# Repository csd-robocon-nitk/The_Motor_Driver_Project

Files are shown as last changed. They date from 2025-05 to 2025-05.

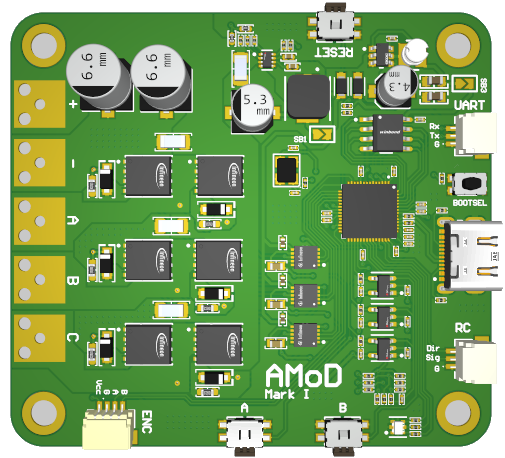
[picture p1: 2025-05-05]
Design/model.png

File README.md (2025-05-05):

# The Motor Driver Project

This project involves creating a smart electronic speed controller (ESC) for both brushed and brushless DC motors.

## Technologies Used

Tech Used

## Team Members

1. [Joel Jojo Painuthara](https://github.com/JoelJojoP)
2. [Sai Aswin Madhavan](https://github.com/MSaiAswin)
3. [Suhas R P](https://github.com/Suhas19822)

## License

This repository is licensed under the [BSD 3-Clause License](/LICENSE)

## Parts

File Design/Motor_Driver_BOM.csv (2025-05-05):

Line # | Quantity | Designator | Name | Footprint | Manufacturer Part Number 1 | Manufacturer 1 | Description
 | 10 | C1, C3, C4, C5, C6, C7, C8, C9, C11, C12 | 0.1 µF | CAP 0201_0603 | 885012104003 | Wurth Electronics | CAP CER 0.1UF 6.3V X5R 0201
 | 2 | C2, C10 | 1 µF | CAP 0201_0603 | 885012104011 | Wurth Electronics | CAP CER 1UF 6.3V X5R 0201
 | 2 | C13, C14 | 15 pF | CAP 0201_0603 | 885012004006 | Wurth Electronics | CAP CER 15PF 25V C0G/NP0 0201
 | 1 | C15 | 0.1 µF | CAP 0402_1005 | 885012205085 | Wurth Electronics | CAP CER 0.1UF 25V X7R 0402
 | 4 | C16, C38, C39, C40 | 10 µF | CAP 1206_3216 - 0.8MM | 885012108022 | Wurth Electronics | CAP CER 10UF 50V X5R 1206
 | 1 | C17 | 33 µF | CAP ALSMD 5.3MM H5.4MM | EEE-1CA330WAR | Panasonic | CAP ALUM 33UF 20% 16V SMD
 | 1 | C18 | 0.033 µF | CAP 0402_1005 | 885012205015 | Wurth Electronics | CAP CER 0.033UF 10V X7R 0402
 | 1 | C19 | 0.1 µF | CAP 0201_0603 | 885012104001 | Wurth Electronics | CAP CER 0.1UF 16V X5R 0201
 | 2 | C20, C21 | 100 µF | CAP ALSMD 6.6MM H8.0MM | EEEFK1V101XP | Panasonic | CAP ALUM 100UF 20% 35V SMD
 | 1 | C22 | 10 µF | CAP ALSMD 4.3MM H5.4MM | 865060340001 | Wurth Electronics | CAP ALUM 10UF 20% 16V SMD
 | 2 | C23, C24 | 22 µF | MURATA GRM188 0603_1608 | GRM188R60J226MEA0D | Murata | CAP CER 22UF 6.3V X5R 0603
 | 3 | C25, C26, C29 | 0.22 µF | CAP 0603_1608 | 885012206073 | Wurth Electronics | CAP CER 0.22UF 25V X7R 0603
 | 3 | C27, C28, C30 | 1 µF | MURATA GRM155 0402_1005 | GRM155R61E105KA12D | Murata | CAP CER 1UF 25V X5R 0402
 | 7 | C31, C32, C33, C34, C35, C36, C37 | 1000 pF | CAP 0201_0603 | 885012204006 | Wurth Electronics | CAP CER 1000PF 25V X7R 0201
 | 1 | D1 | 19-337C/RSBHGHC-A88/4T | FP-19-337C-RSBHGHC-A88-4T-MFG | 19-337C/RSBHGHC-A88/4T | Everlight | LED Tri-Color 468nm/518nm/632nm 6-Pin SMD-B T/R
 | 2 | D2, D3 | RB160VAM-60TR | RB160VAM-60TR-Footprint-1 | RB160VAM-60TR | Rohm | DIODE SCHOTTKY 60V 1A TUMD2M
 | 6 | D4, D5, D6, D7, D8, D9 | 1N5819HW1-7-F | SOD123F | 1N5819HW1-7-F | Diodes | DIODE SBR 40V 1A SOD123F
 | 1 | J2 | DX07S016JA1R1500 | FP-DX07S016JA1R1500-MFG | DX07S016JA1R1500 | JAE Electronics | USB Connector, 16 Contact(s), Female, Right Angle, Surface Mount Terminal, Locking, Receptacle
 | 1 | L1 | SRP5020TA-8R2M | SRP5020TA-8R2M-Footprint-1 | SRP5020TA-8R2M | Bourns | Ind Chip Power Shielded Wirewound 8.2uH 20% 100KHz 21Q-Factor Metal 2.3A T/R
 | 1 | L2 | SDR0302-3R9ML | SDR0302-3R9ML-Footprint-1 | SDR0302-3R9ML | Bourns | Inductor Power Wirewound 3.9uH 20% 1KHz 24Q-Factor Ferrite 1.3A 120mOhm DCR T/R
 | 1 | P1 | SM04B-SRSS-TB(LF)(SN) | SM04B-SRSS-TB(LF)(SN)-Footprint-1 | SM04B-SRSS-TB | JST | Connector Header, Side Entry, SR Series, 4 Position, 1.00mm, 50V, Surface Mount, Tin, Natural
 | 2 | P2, P3 | SM03B-SRSS-TB(LF)(SN) | JST-SM03B-SRSS-TB_V | SM03B-SRSS-TB | JST | Connector Header, Side Entry, SR Series, 3 Position, 1.00mm, 50V, Surface Mount, Tin, Natural
 | 6 | Q1, Q2, Q3, Q4, Q5, Q6 | BSC027N06LS5ATMA1 | FP-PG-TDSON-8-MFG | BSC027N06LS5ATMA1 | Infineon | Transistor Mosfet N-ch 60V 100A 8-PIN Tdson T/r
 | 3 | R1, R2, R5 | 27 Ohms | YAGEO RES 0201_0603 | RC0201FR-0727RL | Yageo | RES 27 OHM 1% 1/20W 0201
 | 1 | R3 | 1 kOhms | YAGEO RES 0201_0603 | RC0201FR-131KL | Yageo | RES 1K OHM 1% 1/20W 0201
 | 1 | R4 | 75 Ohms | YAGEO RES 0201_0603 | RC0201FR0775RL | Yageo | RES 75 OHM 1% 1/20W 0201
 | 1 | R6 | 5.6 kOhms | YAGEO RES 0201_0603 | RC0201FR-135K6L | Yageo | RES 5.6K OHM 1% 1/20W 0201
 | 1 | R7 | 5.6 Ohms | YAGEO RES 0201_0603 | RC0201FR-075R6L | Yageo | RES 5.6 OHM 1% 1/20W 0201
 | 8 | R8, R17, R28, R31, R32, R33, R34, R35 | 10 kOhms | YAGEO RES 0201_0603 | RC0201FR-0710KL | Yageo | RES 10K OHM 1% 1/20W 0201
 | 2 | R9, R10 | 5.1 kOhms | YAGEO RES 0201_0603 | RC0201FR075K1L | Yageo | RES 5.1K OHM 1% 1/20W 0201
 | 1 | R11 | 68 kOhms | YAGEO RES 0402_1005 | RC0402FR-0768KL | Yageo | RES 68K OHM 1% 1/16W 0402
 | 1 | R12 | 10 kOhms | YAGEO RES 0402_1005 | RC0402FR-0710KL | Yageo | RES 10K OHM 1% 1/16W 0402
 | 1 | R13 | 309 kOhms | YAGEO RES 0201_0603 | RC0201FR-07309KL | Yageo | RES 309K OHM 1% 1/20W 0201
 | 1 | R14 | 130 kOhms | YAGEO RES 0201_0603 | RC0201JR-07130KL | Yageo | RES 130K OHM 5% 1/20W 0201
 | 1 | R15 | 38.3 kOhms | YAGEO RES 0201_0603 | RC0201FR-0738K3L | Yageo | RES 38.3K OHM 1% 1/20W 0201
 | 1 | R16 | 9.09 kOhms | YAGEO RES 0201_0603 | RC0201FR-079K09L | Yageo | RES 9.09K OHM 1% 1/20W 0201
 | 6 | R18, R19, R20, R21, R22, R23 | 10 Ohms | YAGEO RES 0603_1608 | RC0603JR-0710RL | Yageo | RES 10 OHM 5% 1/10W 0603
 | 6 | R24, R25, R26, R27, R29, R30 | 47 kOhms | YAGEO RES 0201_0603 | RC0201FR-0747KL | Yageo | RES 47K OHM 1% 1/20W 0201
 | 1 | R36 | 1 kOhms | YAGEO RES 0201_0603 | RC0201JR-071KP | Yageo | RES 1K OHM 5% 1/20W 0201
 | 3 | S1, S2, S3 | EVQ-PUC02K | PANASONIC EVQPUC | EVQ-PUC02K | Panasonic | SWITCH TACTILE SPST-NO 0.05A 12V
 | 1 | S4 | KMR741NG ULC LFS | C&K KMR7 | KMR741NGULCLFS | ITT C&K | SWITCH TACTILE SPST-NO 50MA 32V
 | 1 | U1 | RP2040 | QFN40P700X700X90-57N | SC0914(7) | Raspberry Pi | ARM Microcontrollers - MCU IC RP2040 (RP2B2) T&R, 500 (7" reel)
 | 1 | U2 | TPS62932DRLR | FP-DRL0008A-MFG | TPS62932DRLR | Texas Instruments | 3.8-V to 30-V input, 2-A, 200-kHz to 2.2-MHz, low-IQ synchronous buck converter in SOT-583 package 8-SOT-5X3 -40 to 150
 | 1 | U3 | AP63203WU-7 | FP-TSOT26-MFG | AP63203WU-7 | Diodes | AP63203 Series 3.3 V 2 A SMT Fixed Low IQ Synchronous Buck - TSOT-26
 | 3 | U4, U5, U6 | 2ED2732S01G | SON50P300X300X90-11N-1 | 2ED2732S01GXTMA1 | Infineon | Half Bridge SOI Gate Driver with Integrated Bootstrap Diode
 | 3 | U7, U8, U9 | LMV321IDBVR | FP-DBV0005A-IPC_B | LMV321IDBVR | Texas Instruments | Single, 5.5-V, 1-MHz, RRO operational amplifier 5-SOT-23 -40 to 125
 | 1 | U10 | W25Q16JVSNIQ | FP-W25Q16JVSNIQ_TR-IPC_B | W25Q16JVSNIQ TR | Winbond | NOR Flash Serial (SPI, Dual SPI, Quad SPI) 3V/3.3V 16M-bit 2M x 8 6ns Automotive 8-Pin SOIC N T/R
 | 1 | Y1 | 12MHz | ABRACON ABM8G | ABM8G-12.000MHZ-B4Y-T | Abracon | CRYSTAL 12.0000MHZ 10PF SMD

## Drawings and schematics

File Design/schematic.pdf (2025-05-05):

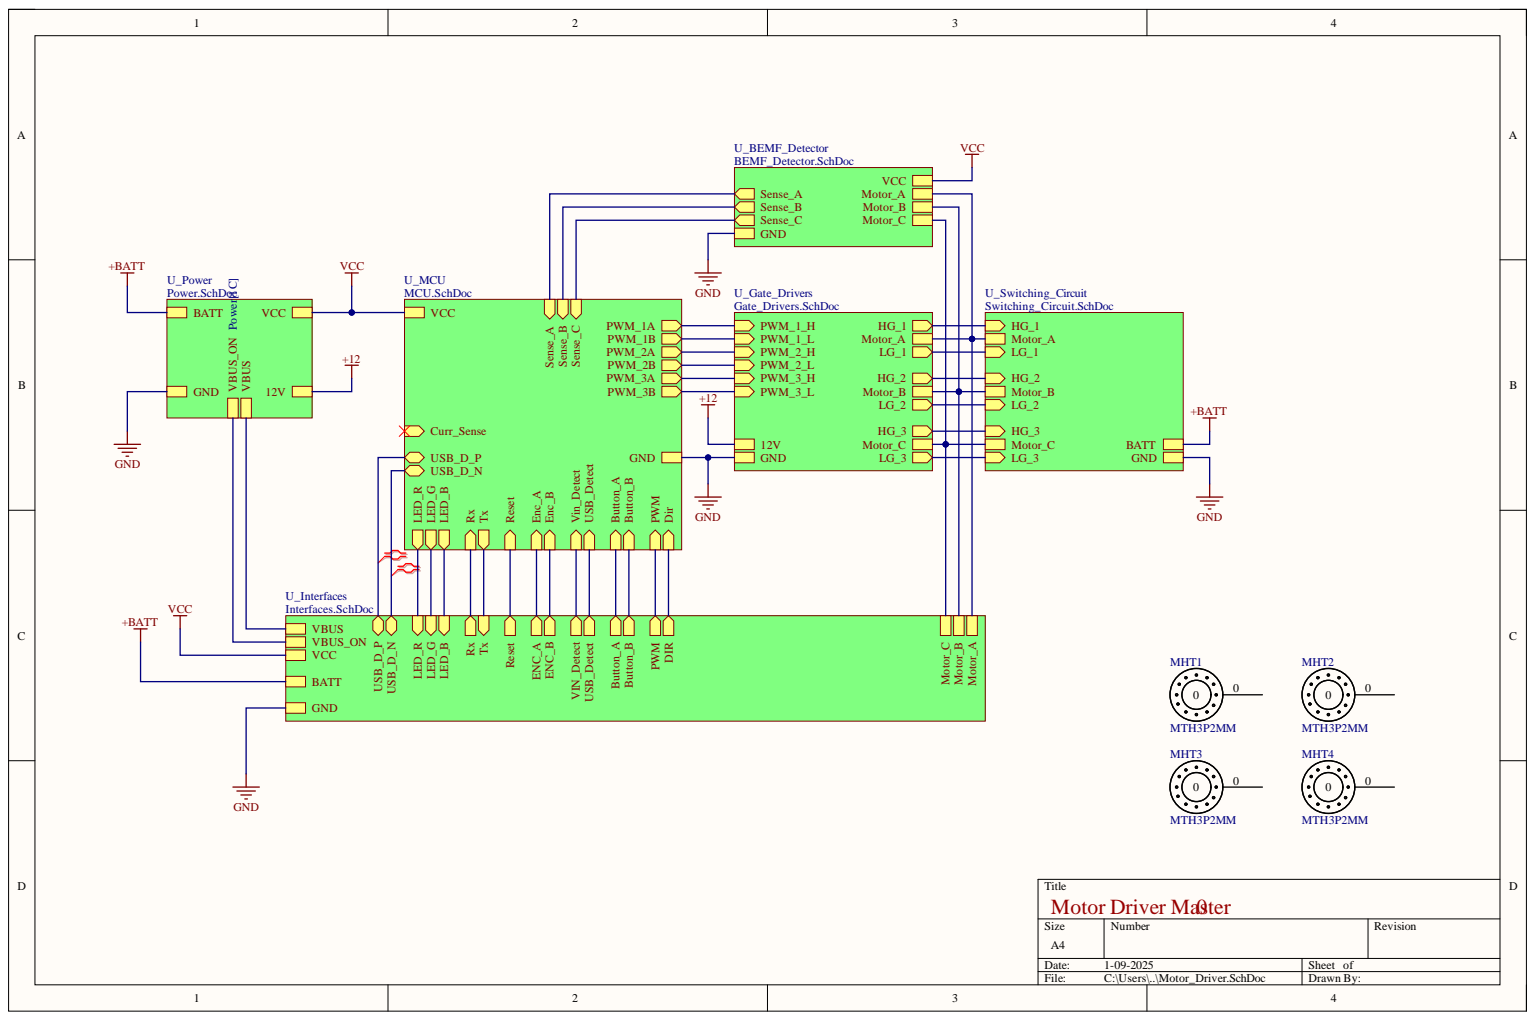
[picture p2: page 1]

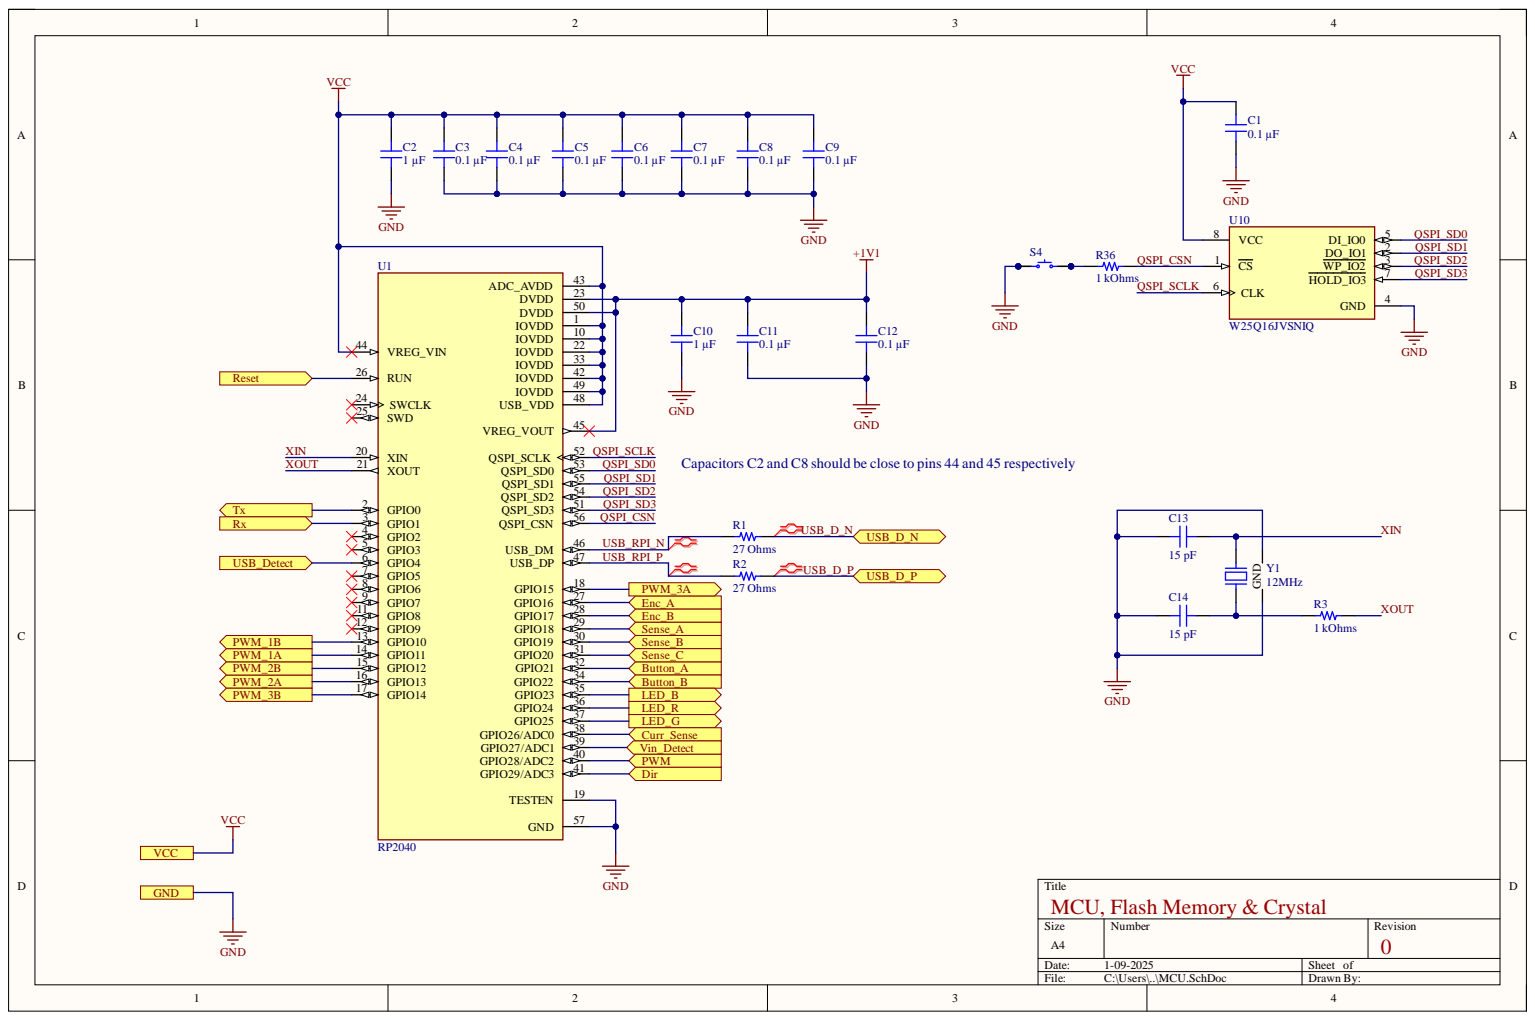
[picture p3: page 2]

Capacitors C2 and C8 should be close to pins 44 and 45 respectively

Title
MCU, Flash Memory & Crystal

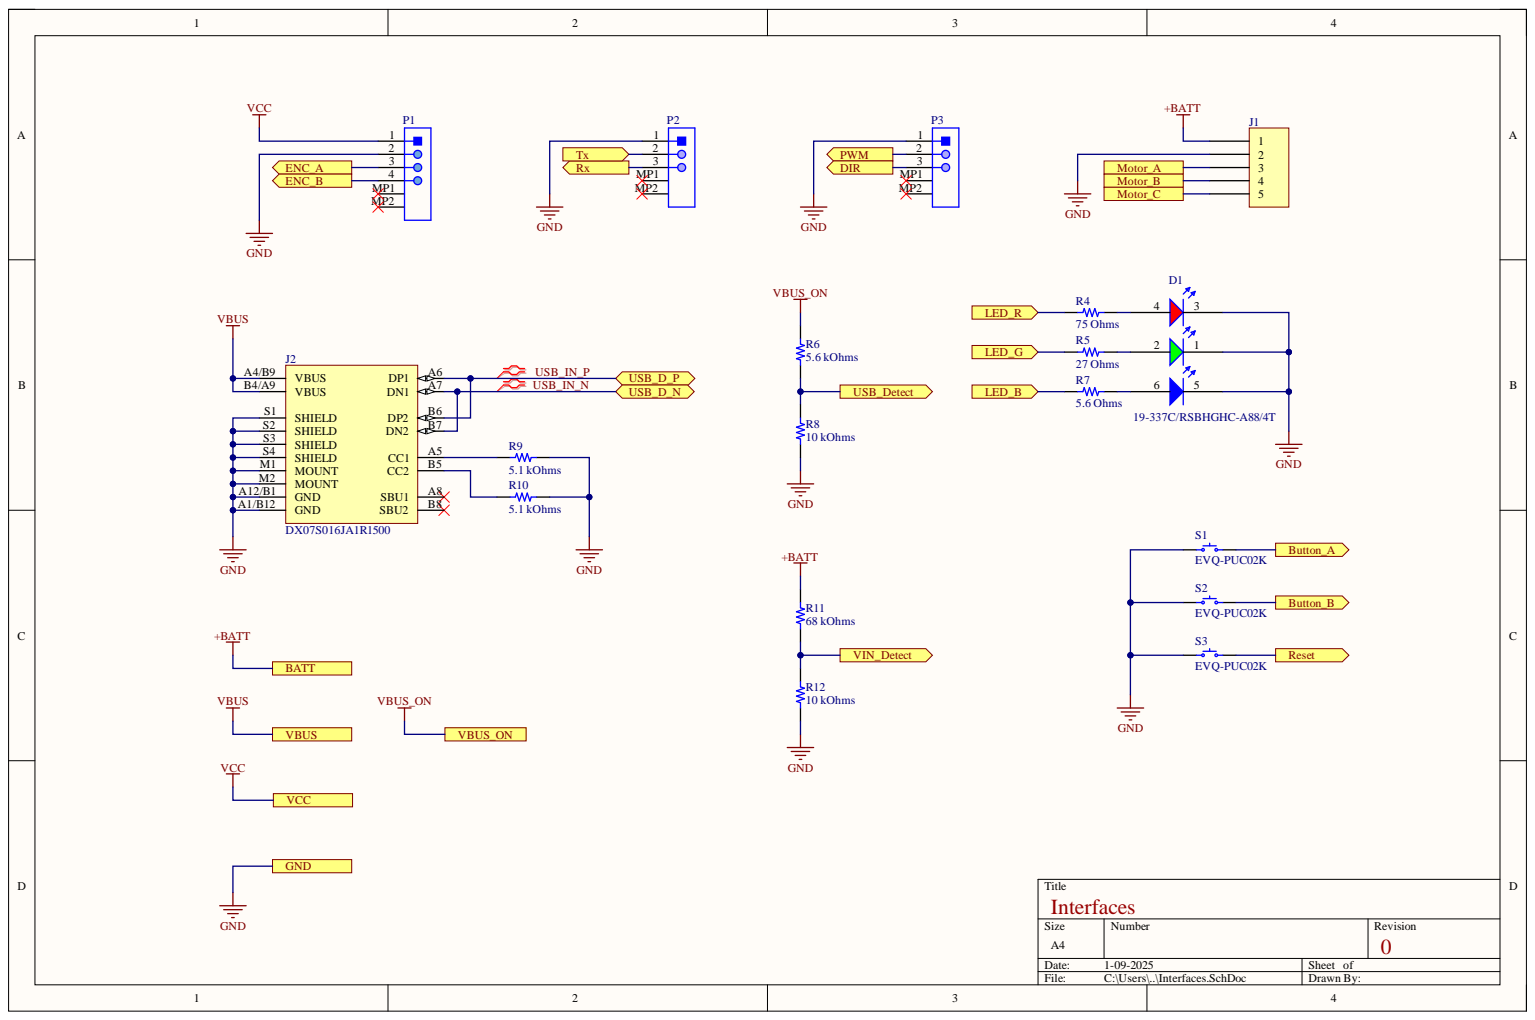
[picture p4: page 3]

SHIELD S2

SHIELD S4

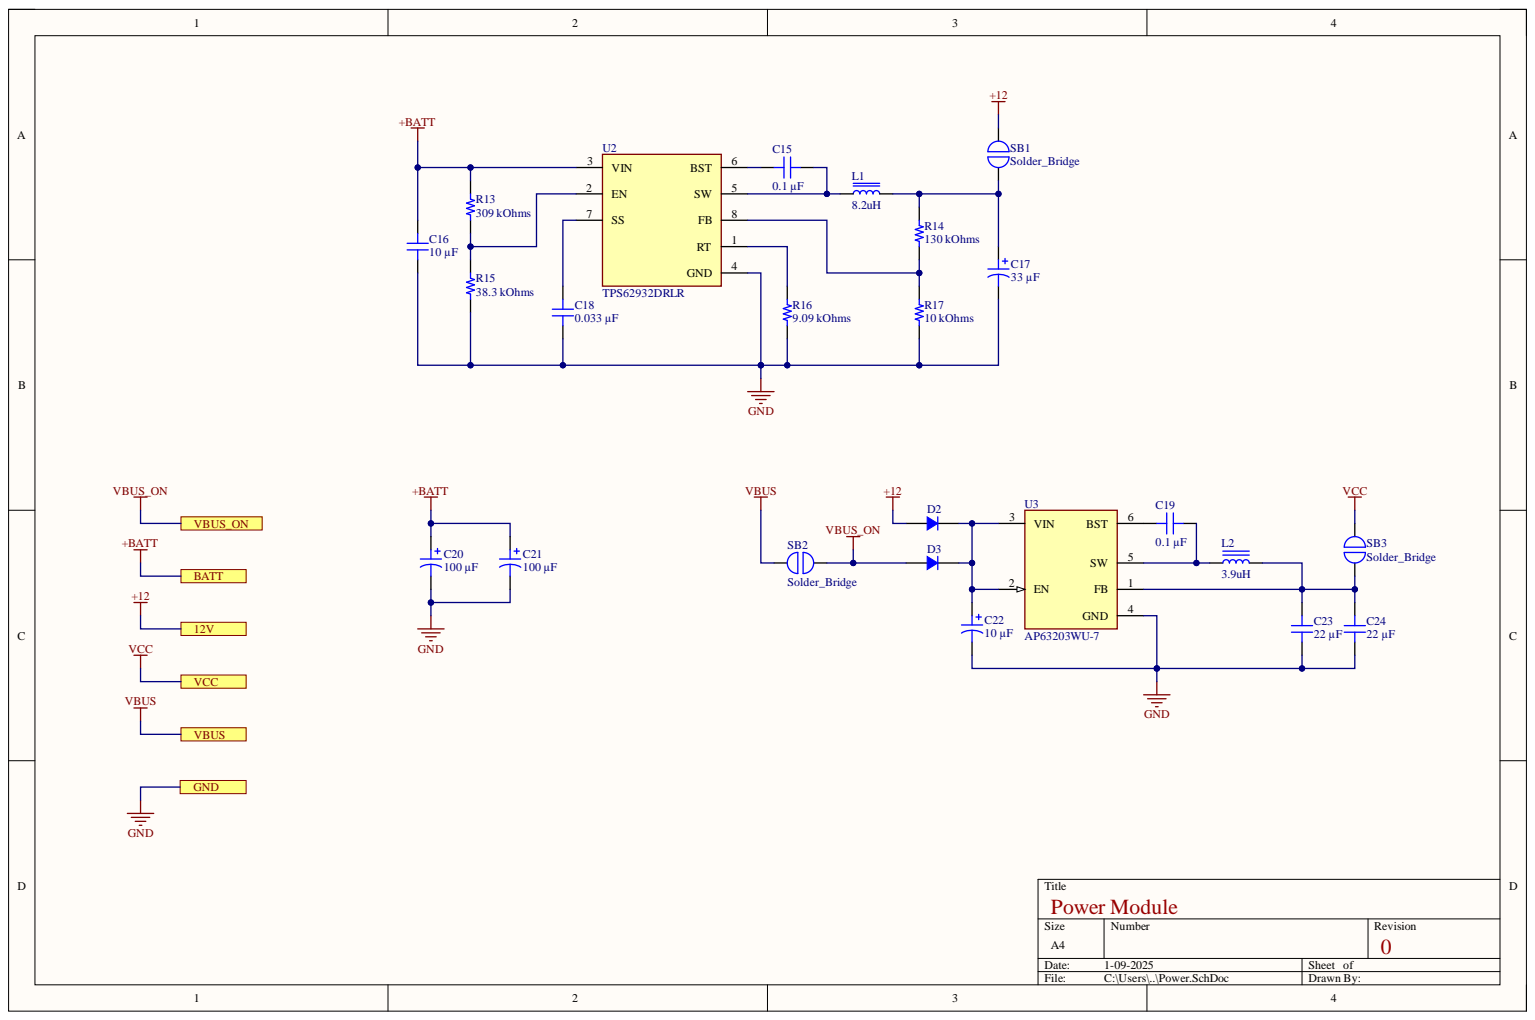
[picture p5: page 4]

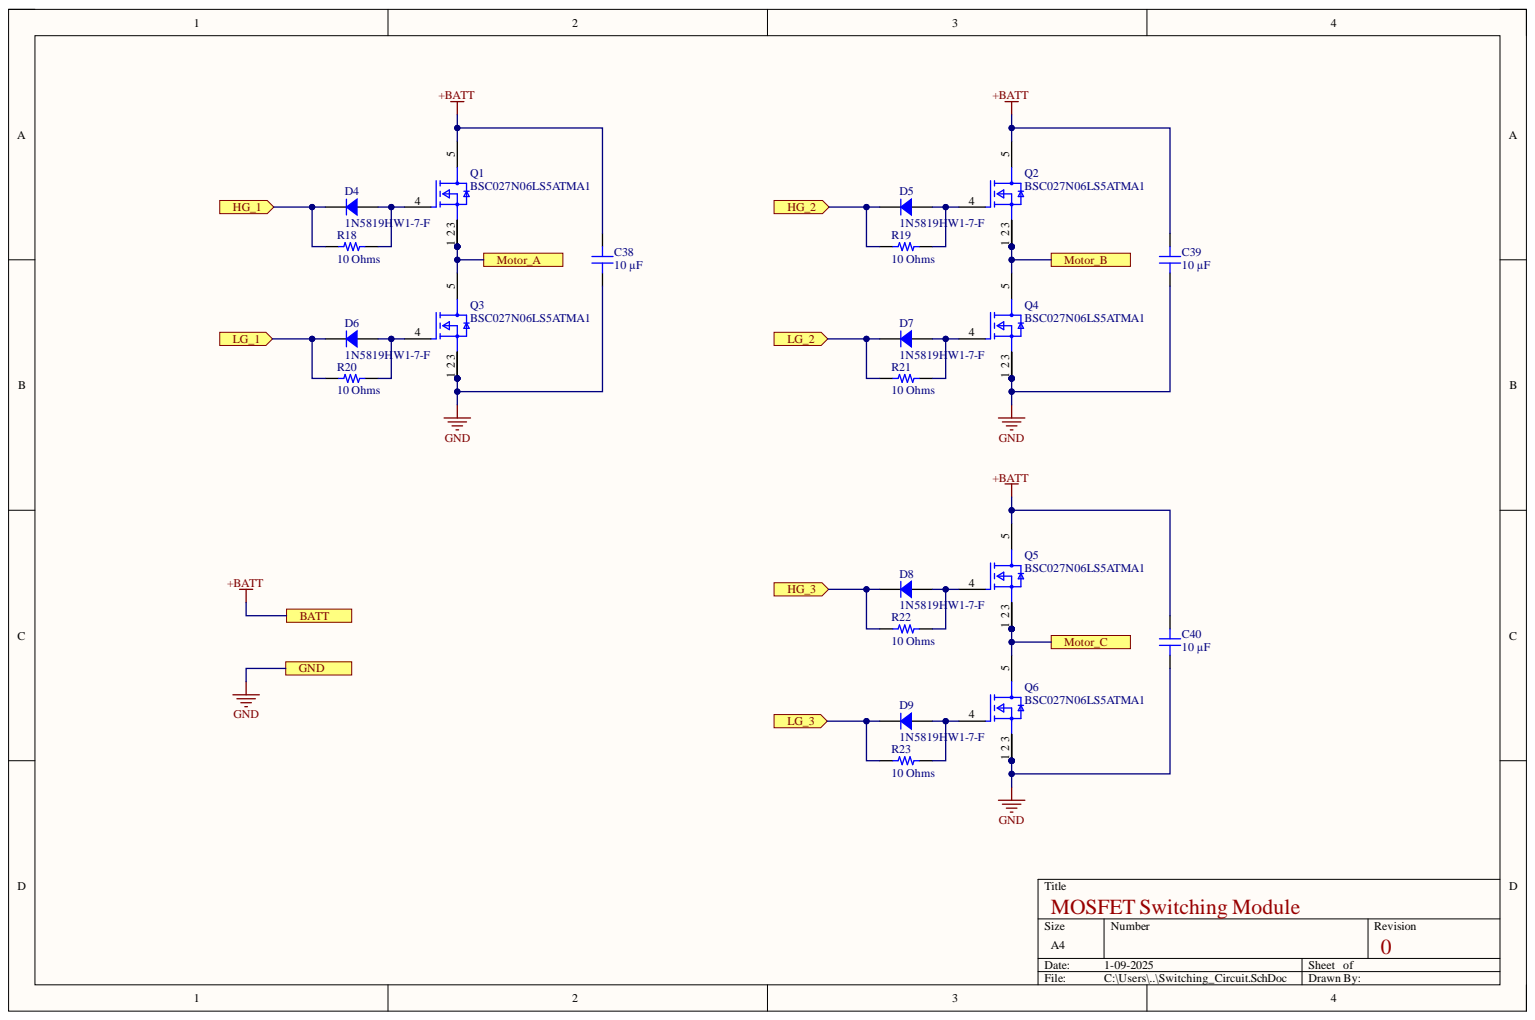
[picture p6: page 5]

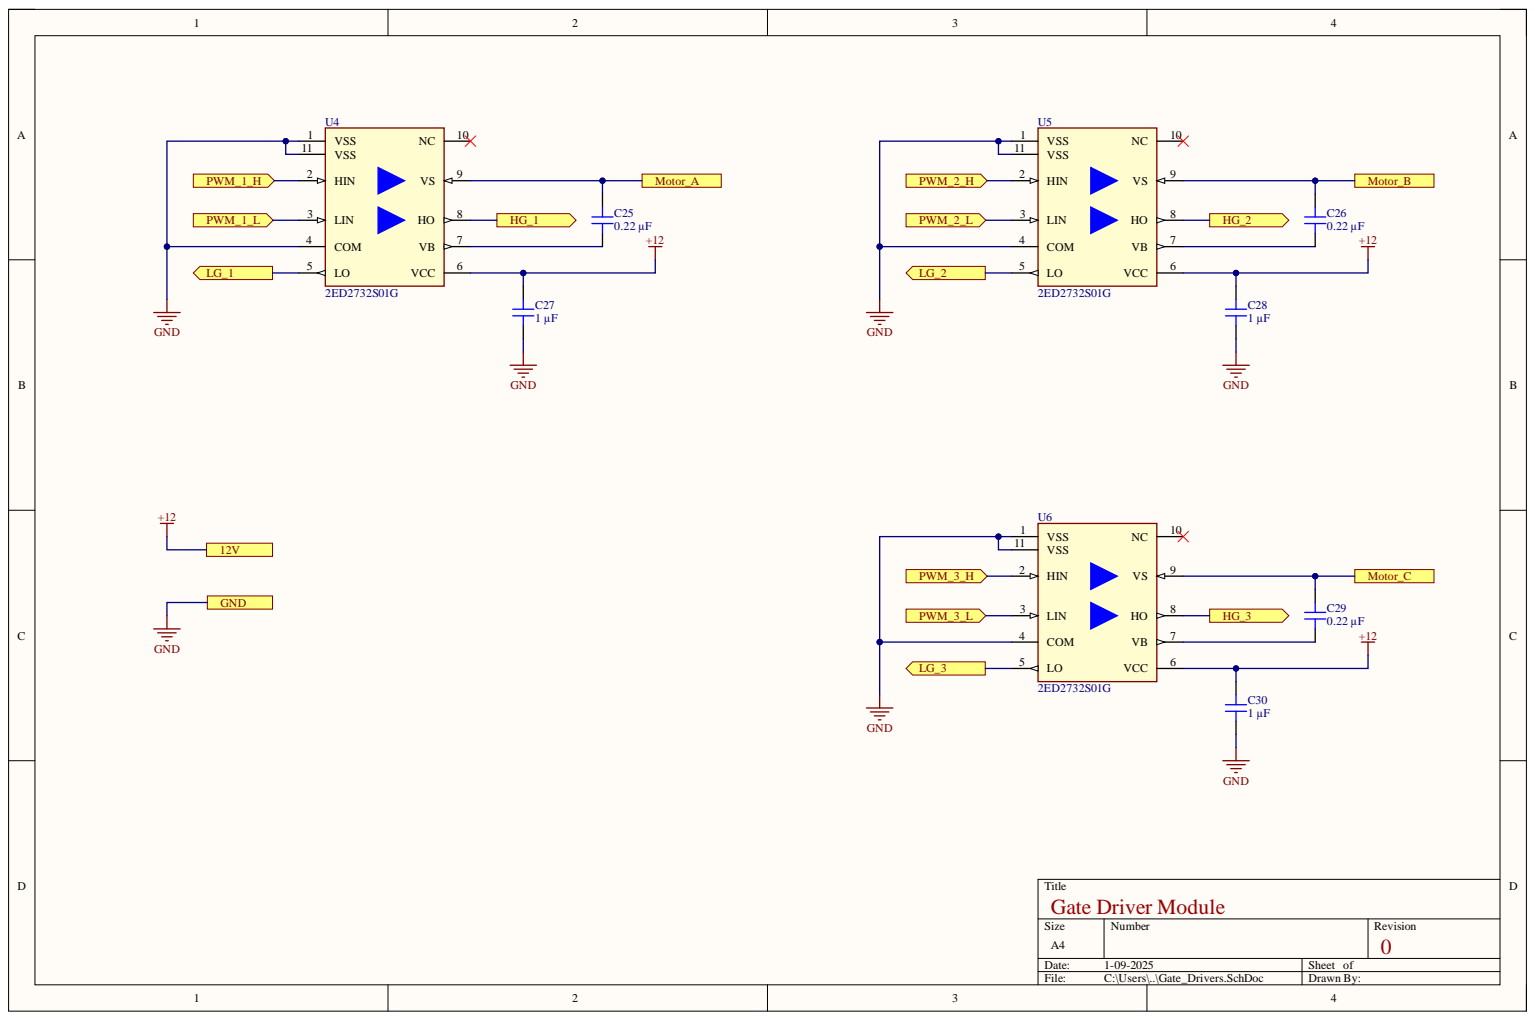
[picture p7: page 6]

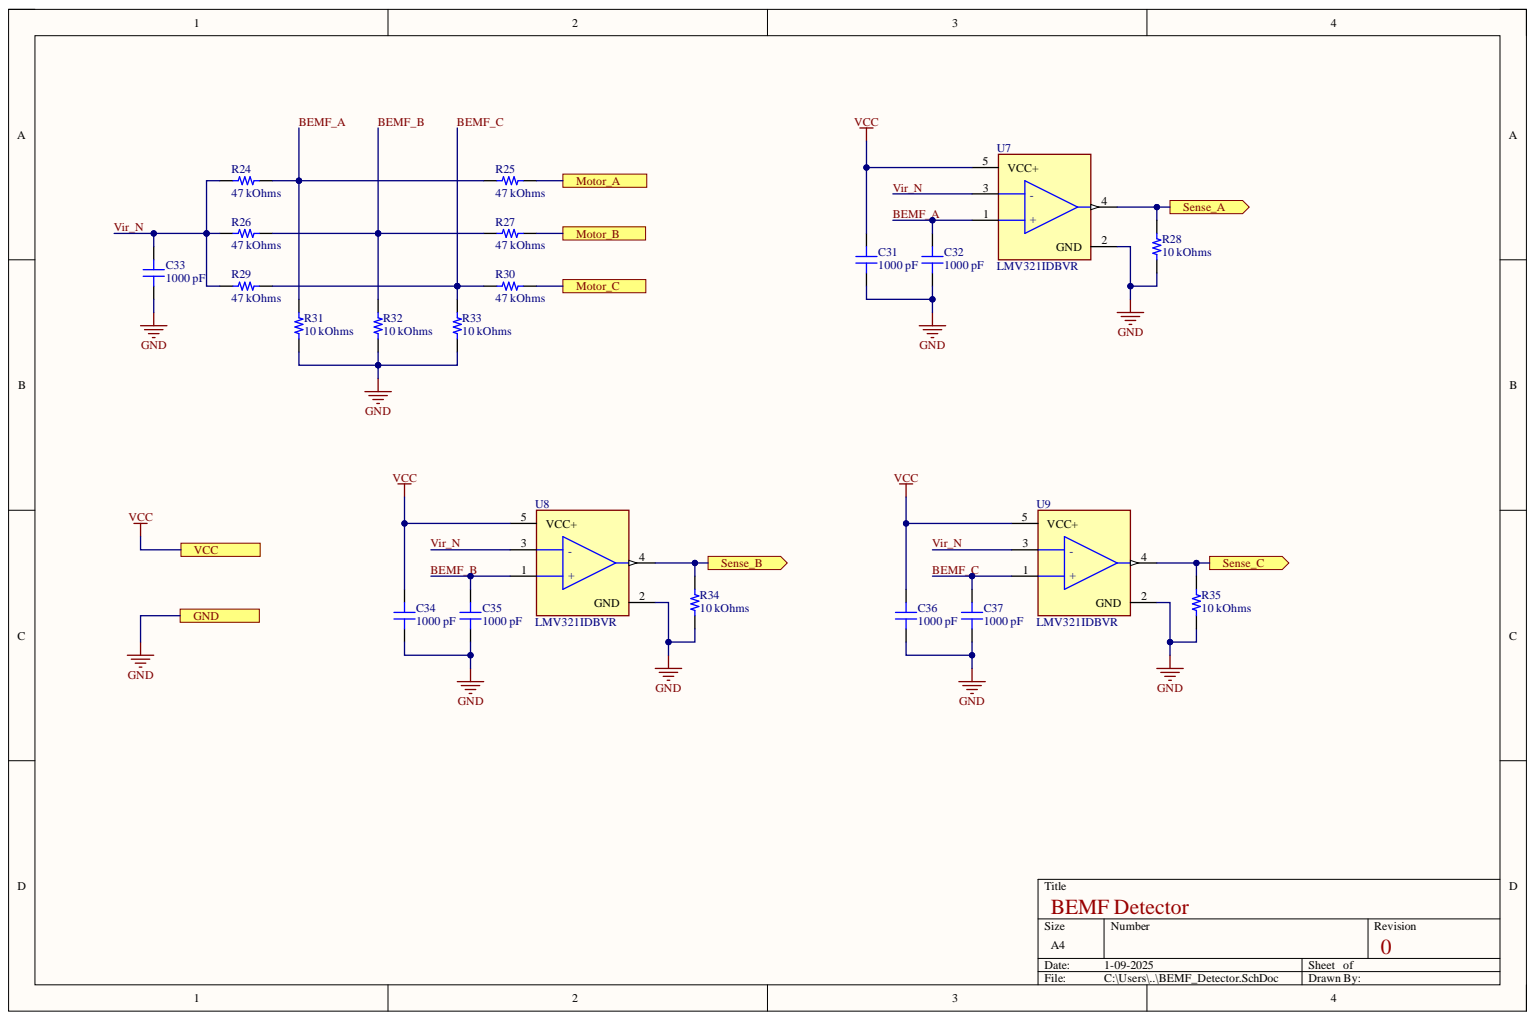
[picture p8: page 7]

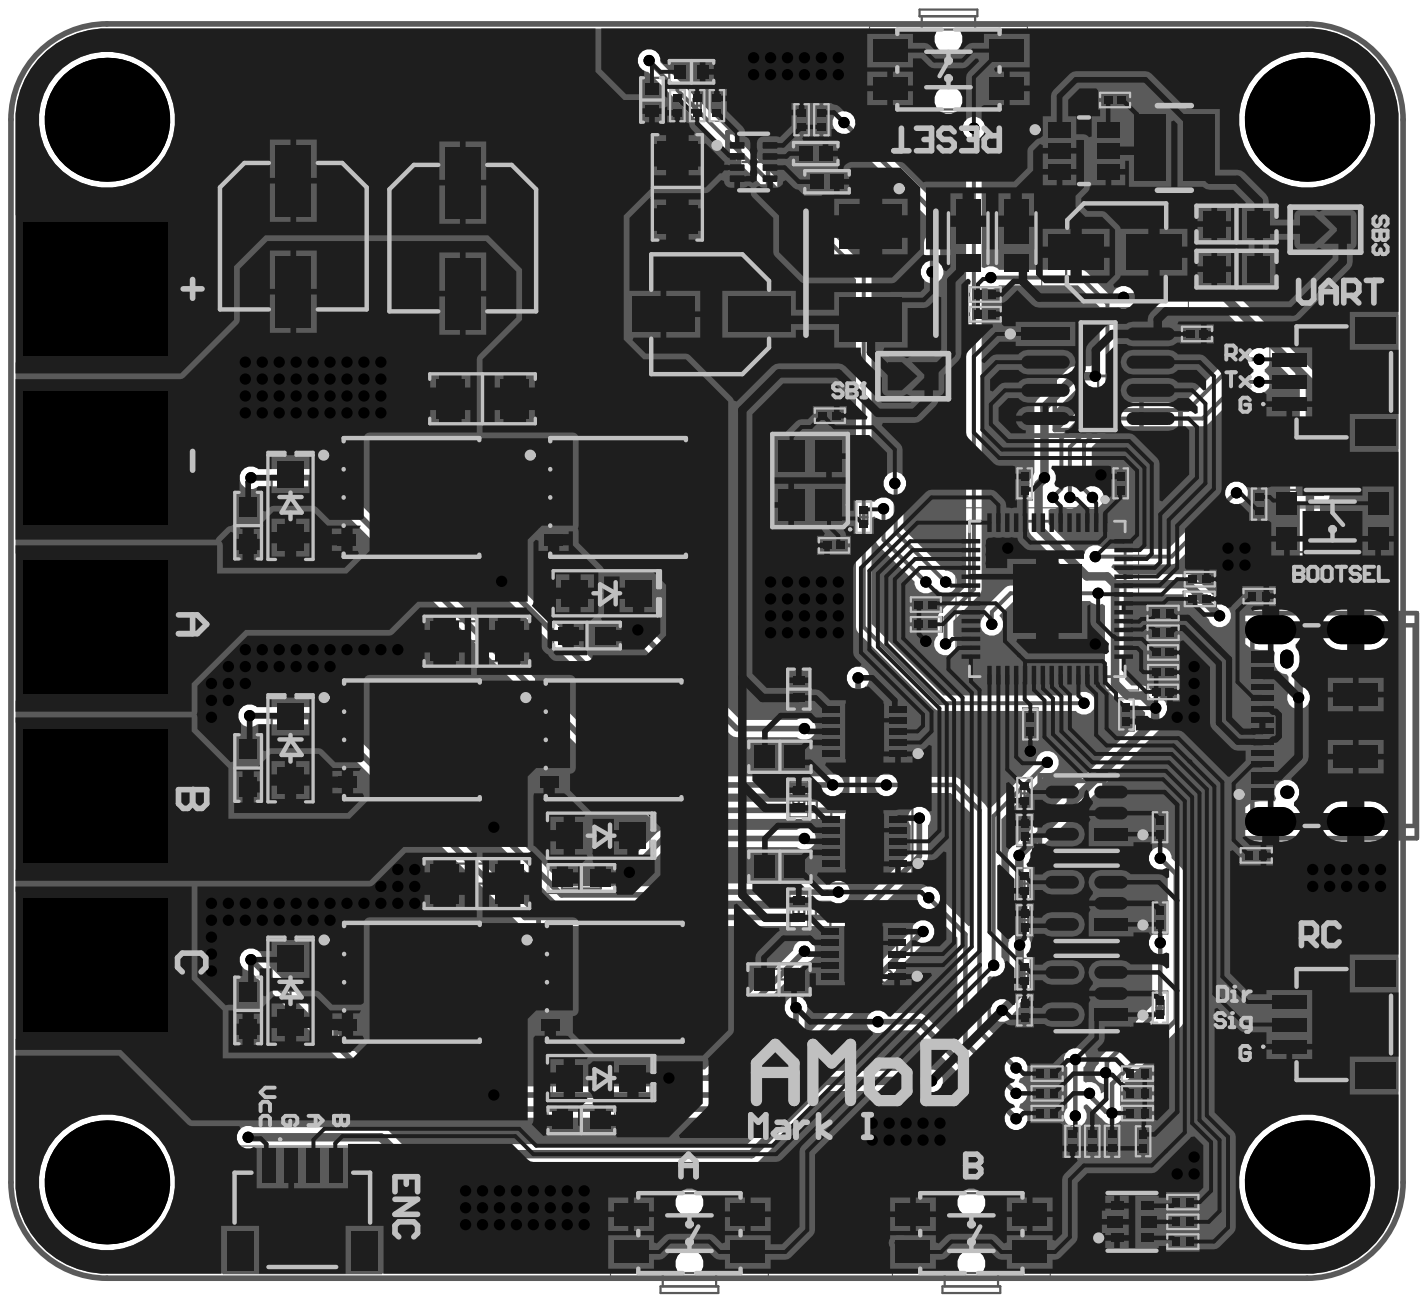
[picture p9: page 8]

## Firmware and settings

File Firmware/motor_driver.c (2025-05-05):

#include <stdio.h>

#include "config.h"
#include "utilities.h"

#if BLDC_MODE
#include "bldc_drive.h"
#elif BDC_MODE
#include "bdc_drive.h"
#endif

#if BLDC_MODE && BDC_MODE
#error "BLDC_MODE and BDC_MODE cannot be both set to 1"
#endif
#if !BLDC_MODE && !BDC_MODE
#error "Either one of BLDC_MODE or BDC_MODE must be set to 1"
#endif

#if ANALOG_INPUT && UART_INPUT && USB_SERIAL_INPUT
#error "Only one of ANALOG_INPUT, UART_INPUT, or USB_SERIAL_INPUT can be set to 1"
#endif
#if !ANALOG_INPUT && !UART_INPUT && !USB_SERIAL_INPUT
#error "Either one of ANALOG_INPUT, UART_INPUT, or USB_SERIAL_INPUT must be set to 1"
#endif

int main()
{
    #if DEBUG_EN || USB_SERIAL_INPUT
    stdio_init_all();
    #endif

    #if ANALOG_INPUT
    analog_signal_init();
    #endif

    #if UART_INPUT
    uart_signal_init();
    #endif

    #if BLDC_MODE
    bldc_init();
    while (!is_stall)
    {
        #if ANALOG_INPUT
        set_bldc_pwm_from_analog(read_analog_signal());
        #endif
        #if UART_INPUT
        char *uart_val = read_uart_signal();
        set_bldc_pwm_from_uart(uart_val);
        free(uart_val);
        #endif
        #if USB_SERIAL_INPUT
        char *usb_val = read_usb_serial_signal();
        set_bldc_pwm_from_uart(usb_val);
        free(usb_val);
        #endif
        bldc_loop();
    }
    #endif

    #if BDC_MODE
    bdc_init();
    while (true)
    {
        #if ANALOG_INPUT
        set_bdc_pwm_from_analog(read_analog_signal());
        #endif
        #if UART_INPUT
        char *uart_val = read_uart_signal();
        set_bdc_pwm_from_uart(uart_val);
        free(uart_val);
        #endif
        #if USB_SERIAL_INPUT
        char *usb_val = read_usb_serial_signal();
        set_bdc_pwm_from_uart(usb_val);
        free(usb_val);
        #endif
    }
    #endif

    #if DEBUG_EN
    printf(":( Restart ESC\n");
    #endif
    while (true);
    return 0;
}

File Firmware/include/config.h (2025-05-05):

#ifndef CONFIG_H
#define CONFIG_H

// Set to BLDC drive mode
#define BLDC_MODE 1
// Set to BDC drive mode
#define BDC_MODE 0
// Note: Only one of the above modes should be set to 1

// Enable debug data
#define DEBUG_EN 0

// Enable Bi-directional control (for Analog Input Mode)
#define BIDIR_EN 0

// PWM signal cutoff threshold (0 - 4095) (for BLDC Mode)
#define PWM_THRESH 1000

// Open loop timing at PWM cutoff (for BLDC Mode)
#define OPEN_LOOP_TIME 3675

// Stall detection threshold (in ms) (for BLDC Mode)
#define STALL_THRESH 5

// Stall recovery attempts (for BLDC Mode)
#define STALL_RECOVERY_ATTEMPTS 3

// Signal Input Mode
#define ANALOG_INPUT 1
#define UART_INPUT 0
#define USB_SERIAL_INPUT 0
// Note: Only one of the above modes should be set to 1.

// PID Control Enable (for BDC Mode in UART or USB serial Input Mode)
#define PID_EN 0

// PID Update Interval (in ms) (for BDC Mode in UART or USB serial Input Mode)
#define PID_INTERVAL 10

// PID Control Parameters (for BDC Mode in UART or USB serial Input Mode)
#define KP 0.1
#define KI 0.01
#define KD 0.01
#define MAX_SPEED 1000
#define ENC_PPR 100

#endif // CONFIG_H

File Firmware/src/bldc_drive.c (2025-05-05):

#include "bldc_drive.h"

volatile int8_t bldc_step = 0;
volatile bool is_start = true;
volatile bool is_stall = false;
int stall_count = 0;
alarm_id_t stall_alarm;
uint16_t target_pwm = 0;
uint16_t bldc_pwm = 0;
Motor_Dir bldc_dir = MOTOR_DIR_CW;
uint32_t cur_time = 0;
uint32_t prev_time = 0;

void bldc_init()
{
    #if DEBUG_EN
    printf("Setup GPIO for BEMF Detection\n");
    #endif
    gpio_init_mask(1 << sensor_A | 1 << sensor_B | 1 << sensor_C);
    gpio_set_dir_in_masked(1 << sensor_A | 1 << sensor_B | 1 << sensor_C);

    #if DEBUG_EN
    printf("Enable GPIO for PWM Generation\n");
    #endif
    gpio_init_mask(1 << phase_A_low | 1 << phase_B_low | 1 << phase_C_low);
    gpio_set_dir_out_masked(1 << phase_A_low | 1 << phase_B_low | 1 << phase_C_low);
    gpio_set_function_masked(1 << phase_A_high | 1 << phase_B_high | 1 << phase_C_high, GPIO_FUNC_PWM);
    uint slice_num_1 = pwm_gpio_to_slice_num(phase_A_high);
    uint slice_num_2 = pwm_gpio_to_slice_num(phase_B_high);
    uint slice_num_3 = pwm_gpio_to_slice_num(phase_C_high);
    pwm_set_freq(slice_num_1, 31000);
    pwm_set_freq(slice_num_2, 31000);
    pwm_set_freq(slice_num_3, 31000);
    pwm_set_output_polarity(slice_num_1, false, false);
    pwm_set_output_polarity(slice_num_2, false, false);
    pwm_set_output_polarity(slice_num_3, false, false);
    pwm_set_mask_enabled(1 << slice_num_1 | 1 << slice_num_2 | 1 << slice_num_3);
    pwm_set_gpio_level(phase_A_high, 0);
    pwm_set_gpio_level(phase_B_high, 0);
    pwm_set_gpio_level(phase_C_high, 0);

    #if DEBUG_EN
    printf("Setup BEMF Interrupt\n");
    #endif
    gpio_set_irq_enabled_with_callback(sensor_A, GPIO_IRQ_EDGE_RISE, false, update_step);
    gpio_set_irq_enabled_with_callback(sensor_A, GPIO_IRQ_EDGE_FALL, false, update_step);
    gpio_set_irq_enabled_with_callback(sensor_B, GPIO_IRQ_EDGE_RISE, false, update_step);
    gpio_set_irq_enabled_with_callback(sensor_B, GPIO_IRQ_EDGE_FALL, false, update_step);
    gpio_set_irq_enabled_with_callback(sensor_C, GPIO_IRQ_EDGE_RISE, false, update_step);
    gpio_set_irq_enabled_with_callback(sensor_C, GPIO_IRQ_EDGE_FALL, false, update_step);

    #if DEBUG_EN
    printf("Charging the Bootstrap Capacitor\n");
    #endif
    gpio_put(phase_A_low, phase_Al_high);
    gpio_put(phase_B_low, phase_Bl_high);
    gpio_put(phase_C_low, phase_Cl_high);
    sleep_ms(1000);
    gpio_put(phase_A_low, phase_Al_low);
    gpio_put(phase_B_low, phase_Bl_low);
    gpio_put(phase_C_low, phase_Cl_low);

    #if DEBUG_EN
    printf("Initialization Complete\n");
    #endif
}

int64_t stall_protection(alarm_id_t id, __unused void *user_data)
{
    #if DEBUG_EN
    printf("Stall Detected\n");
    #endif
    stall_count++;
    bldc_pwm = 0;
    cancel_alarm(stall_alarm);
}

void update_step(uint gpio, uint32_t event_mask)
{
    if (bldc_pwm > PWM_THRESH)
    {
        cancel_alarm(stall_alarm);
        stall_alarm = add_alarm_in_ms(STALL_THRESH, stall_protection, NULL, false);
    }
    if (!is_start)
    {
        bldc_step++;
        bldc_step %= 6;
        if(bldc_dir  == MOTOR_DIR_CW)
            bldc_move_cw();
        else
            bldc_move_ccw();
    }
}

void bldc_move_cw()
{
    switch (bldc_step)
    {
    case 0:
        pwm_set_gpio_level(phase_C_high, 0);
        pwm_set_gpio_level(phase_A_high, bldc_pwm);
        gpio_put(phase_B_low, phase_Bl_high);
        gpio_put(phase_A_low, phase_Al_low);
        gpio_set_irq_enabled_with_callback(sensor_A, GPIO_IRQ_EDGE_FALL, false, update_step);
        gpio_set_irq_enabled_with_callback(sensor_C, GPIO_IRQ_EDGE_RISE, true, update_step);
        break;
    case 1:
        pwm_set_gpio_level(phase_B_high, 0);
        pwm_set_gpio_level(phase_A_high, bldc_pwm);
        gpio_put(phase_C_low, phase_Cl_high);
        gpio_put(phase_B_low, phase_Bl_low);
        gpio_set_irq_enabled_with_callback(sensor_C, GPIO_IRQ_EDGE_RISE, false, update_step);
        gpio_set_irq_enabled_with_callback(sensor_B, GPIO_IRQ_EDGE_FALL, true, update_step);
        break;
    case 2:
        pwm_set_gpio_level(phase_A_high, 0);
        pwm_set_gpio_level(phase_B_high, bldc_pwm);
        gpio_put(phase_C_low, phase_Cl_high);
        gpio_put(phase_B_low, phase_Bl_low);
        gpio_set_irq_enabled_with_callback(sensor_B, GPIO_IRQ_EDGE_FALL, false, update_step);
        gpio_set_irq_enabled_with_callback(sensor_A, GPIO_IRQ_EDGE_RISE, true, update_step);
        break;
    case 3:
        pwm_set_gpio_level(phase_C_high, 0);
        pwm_set_gpio_level(phase_B_high, bldc_pwm);
        gpio_put(phase_A_low, phase_Al_high);
        gpio_put(phase_C_low, phase_Cl_low);
        gpio_set_irq_enabled_with_callback(sensor_A, GPIO_IRQ_EDGE_RISE, false, update_step);
        gpio_set_irq_enabled_with_callback(sensor_C, GPIO_IRQ_EDGE_FALL, true, update_step);
        break;
    case 4:
        pwm_set_gpio_level(phase_B_high, 0);
        pwm_set_gpio_level(phase_C_high, bldc_pwm);
        gpio_put(phase_A_low, phase_Al_high);
        gpio_put(phase_C_low, phase_Cl_low);
        gpio_set_irq_enabled_with_callback(sensor_C, GPIO_IRQ_EDGE_FALL, false, update_step);
        gpio_set_irq_enabled_with_callback(sensor_B, GPIO_IRQ_EDGE_RISE, true, update_step);
        break;
    case 5:
        pwm_set_gpio_level(phase_A_high, 0);
        pwm_set_gpio_level(phase_C_high, bldc_pwm);
        gpio_put(phase_B_low, phase_Bl_high);
        gpio_put(phase_A_low, phase_Al_low);
        gpio_set_irq_enabled_with_callback(sensor_B, GPIO_IRQ_EDGE_RISE, false, update_step);
        gpio_set_irq_enabled_with_callback(sensor_A, GPIO_IRQ_EDGE_FALL, true, update_step);
        break;
    }
}
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

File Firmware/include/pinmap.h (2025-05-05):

#ifndef PINMAP_H
#define PINMAP_H

// Motor Coil Pins
#define phase_A_high 11
#define phase_A_low 10
#define phase_B_high 13
#define phase_B_low 12
#define phase_C_high 15
#define phase_C_low 14

// BEMF Pins
#define sensor_A 18
#define sensor_B 19
#define sensor_C 20

// GPIO Pin States
#define phase_Al_low  1
#define phase_Al_high 0
#define phase_Bl_low  0
#define phase_Bl_high 1
#define phase_Cl_low  1
#define phase_Cl_high 0

// Encoder Pins
#define encoder_A 8
#define encoder_B 9

// UART Pins
#define uart_tx 0
#define uart_rx 1

// Analog Control Pins
#define signal_in 27

#endif  // PINMAP_H

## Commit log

2024-06-23 Add design and simulation files
    [Motor_Driver_BOM.csv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]
2024-09-12 Updated components and simulation for additional circuits
2024-12-06 Final design complete
    [Motor_Driver_BOM.csv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]
2024-12-07 Add assembly outputs
    [Motor_Driver_BOM.csv, Motor_Driver_Generic_BOM.csv, Pick Place for Motor_Driver.csv]
2024-12-07 Updated gerber
    [Motor_Driver_Copper_Signal_Bot.gbr, Motor_Driver_Copper_Signal_Top.gbr, Motor_Driver_Legend_Bot.gbr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]
2025-01-02 v1.1 update
    [Motor_Driver_BOM.csv, Motor_Driver_Generic_BOM.csv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]
2025-03-22 Added bulk BOM
    [Motor_Driver_Generic_BOM_Extended.csv]
2025-03-22 Added raw code for bldc drive
2025-03-27 added schematics
2025-05-05 Added final code for bldc drive
2025-05-05 Adde new pcb photo
